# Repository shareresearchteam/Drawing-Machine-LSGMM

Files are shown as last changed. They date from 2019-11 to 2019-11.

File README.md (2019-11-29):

# LSGMM (Large-Scale Generative Mark Maker) Project Open-Source Repository

This machine provides the foundation for a human-robot interaction study that examines viewer interest with respect to process-centric and audience-modifiable abstract drawings.  A minimalistic design approach was used to highlight the aesthetic effect of the drawing and the machine’s motion as opposed to its visual presence.  Viewer interaction will manifest in slight, yet immediate and identifiable marks that stitch together a piece over the course of days or even weeks.  Witnessing the arc of a macroscopic structure appear, and the microscopic contributions from past viewers, is fundamental to the research, and the installation as a whole.

Drawing machines, and hanging pen plotters in particular, have been widely implemented by both the art and maker communities.  Harvey Moon’s work integrated satellite images to stitch together map-based abstractions in a similar exhibit.  Mechanically, we look to expand on existing designs by detailing a more scalable infrastructure.  In terms of interaction, we aim to hone the balance between viewer agency and structure.  Inspiration has been taken both from founders of the generative art movement (Manfred Mohr, Frieder Nake) and traditional contemporary abstractionist (Agnes Martin, Ellsworth Kelly, Eva Hesse, Sol Lewitt).  Subsequent works will examine both the mechanical and algorithmic sources of randomness and imperfection to repeated marks.

The current design serves as a baseline for the project goals described above.  It is our hope that others with overlapping goals can utilize or build on the open source software and hardware.

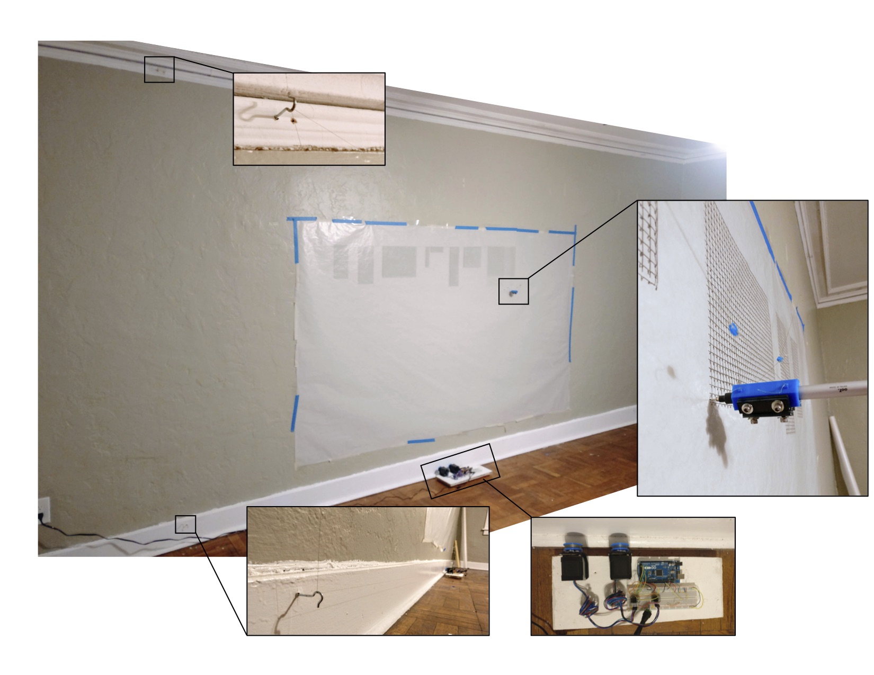
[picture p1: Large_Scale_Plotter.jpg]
Title


## File Guide

**Code Base**:
- Code base used to program Teensy 3.5 micro-controller via the Arduino IDE.  The setup and loop functions are located within the main file LSGMM_code.ino.  The code for the 'Bezier Node' drawing can be found in the node_bezier_alg.ino file.  The code for the 'Worn Structure' drawing can be found in the worn_structue.ino file.
- Libraries used within the LSGMM code base.  Add these to the Library Arduino folder before compilation.

**Hardware Assembly**:
- 3D print models used in LSGMM hardware.  Fusion 360 and .stl files available for all parts.
- Basic assembly instructions
- Bill of Materials 

**Media**:
- Exhibition drawing images of the two designs ('Bezier Node' and 'Worn Structure') from the study exhibitions.
- Introductory project video 

## Reference

A. Phillips, N. Fitter, and A Vinoo, "May I Draw Your Attention?  Initial Lessons from the Large-Scale Generative Mark Maker", Under review for publication in Robotics and Automation Letters (RA-L) and presentation at the 2019 IEEE International Conference on Robotics and Automation (ICRA).

* **Aidan Phillips** - aidan.instance@gmail.com []()
* **Naomi T. Fitter** - naomi.fitter@oregonstate.edu[]()
* **Ashwin Vinoo** - vinooa@oregonstate.edu[]()

## License

This project is licensed under the MIT License - see the [LICENSE.md](LICENSE.md) file for details

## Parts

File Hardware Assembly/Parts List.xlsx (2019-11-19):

Part Description | Purchase Site | QNT | Supplier
NEMA 17 Motors | link (https://www.amazon.com/Stepper-Bipolar-Connector-compatible-Printer/dp/B00PNEQKC0) | 2 | Amazon
ustepper driver | link (https://www.amazon.com/gp/product/B07JPJK8BZ/ref=ppx_yo_dt_b_asin_title_o00__o00_s00?ie=UTF8&psc=1) | 1 | Amazon
Motor dampeners | link (https://www.amazon.com/Rubber-Stepper-Vibration-Damper-Screws/dp/B07415B39B) | 1 | Amazon
Teensy 3.5 uC | link (https://www.digikey.com/product-detail/en/sparkfun-electronics/DEV-14056/1568-1464-ND/6569368) | 1 | Digikey
Shaft Mounting Hub | link (https://www.amazon.com/gp/product/B00KRJAPP4/ref=ox_sc_act_title_1?smid=A333XEUDSX4WY3&psc=1) | 2 | Amazon
Motor right angle brackets | link (https://www.amazon.com/gp/product/B071NWWB7Z/ref=ppx_yo_dt_b_asin_title_o02__o00_s02?ie=UTF8&psc=1) | 1 | Amazon
String | link (https://www.cabelas.com/product/WESTERN-FILAMENT-TUFF-LINE-XP/2972406.uts?productVariantId=6126147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) | 1 | Cabela's
12 V 5A DC PSU | link (https://www.ebay.com/itm/Quality-12V-5A-5-amp-60W-DC-POWER-Supply-ADAPTER-Transformer-LED-Strip-CCTV-PC/123067454133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) | 1 | Amazon

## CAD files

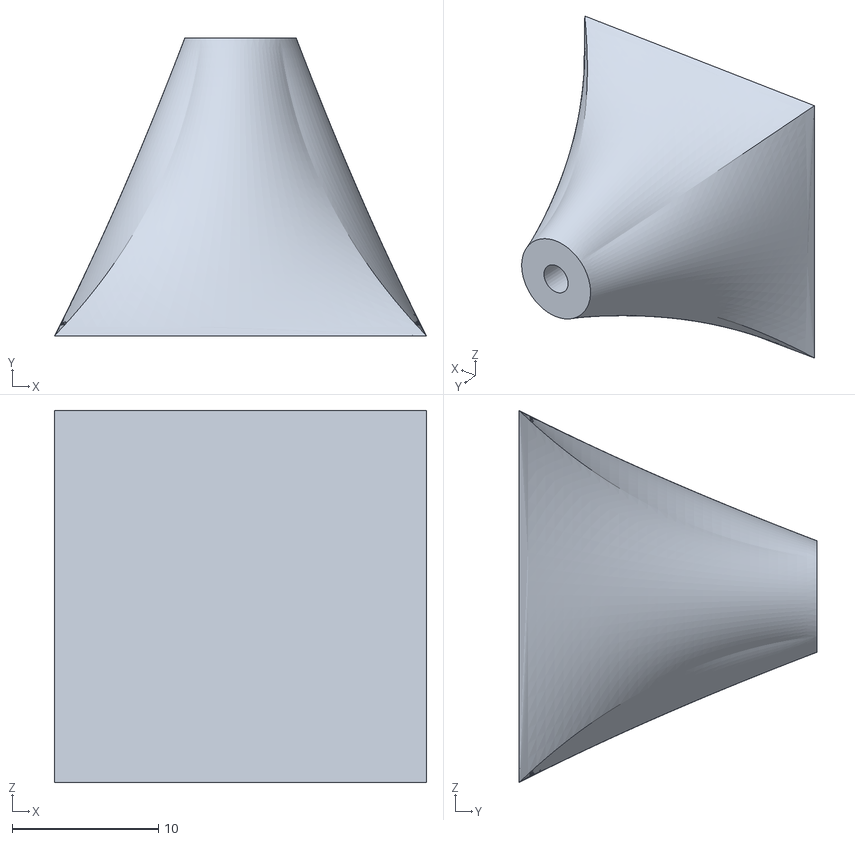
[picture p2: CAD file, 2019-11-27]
Hardware Assembly/3D Print Models/EyeHook Holders.stl
25.4 x 20.3 x 25.4

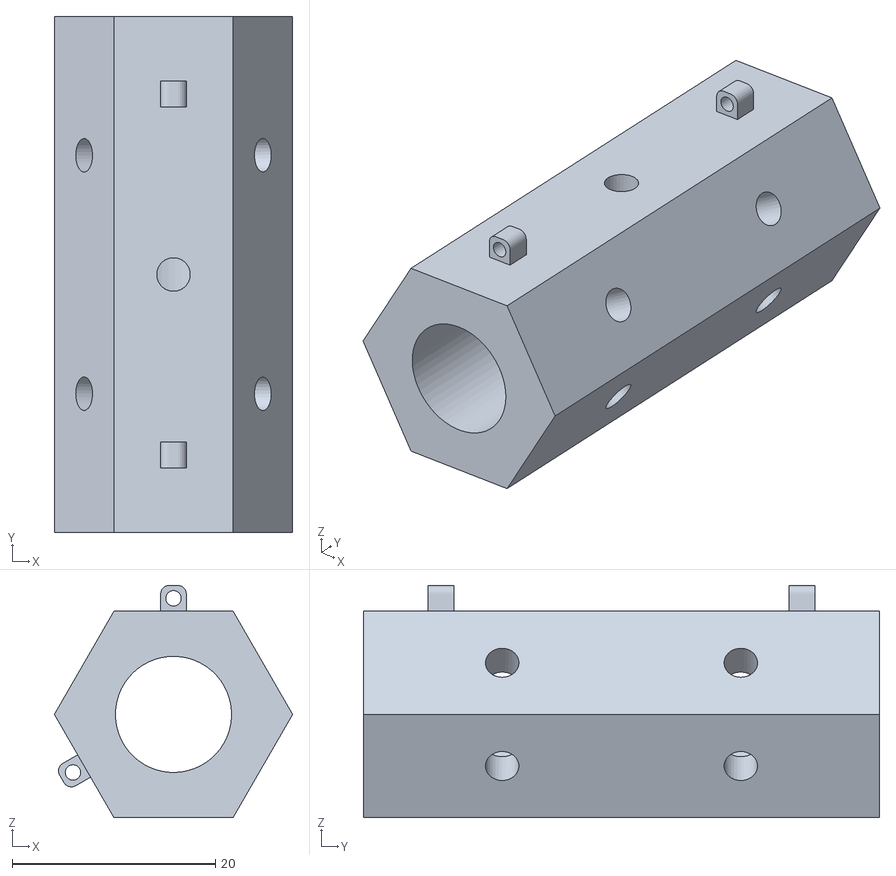
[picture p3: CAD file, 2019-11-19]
Hardware Assembly/3D Print Models/Pen_Holder.stl
23.5 x 50.8 x 22.9

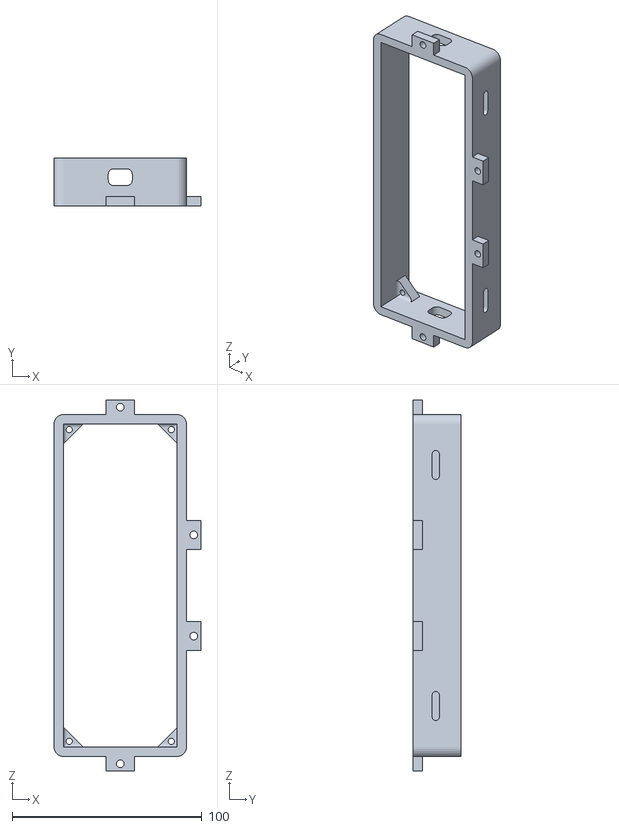
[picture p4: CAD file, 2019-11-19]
Hardware Assembly/3D Print Models/Electronics_Enclosure.stl
77.5 x 25.4 x 195.6

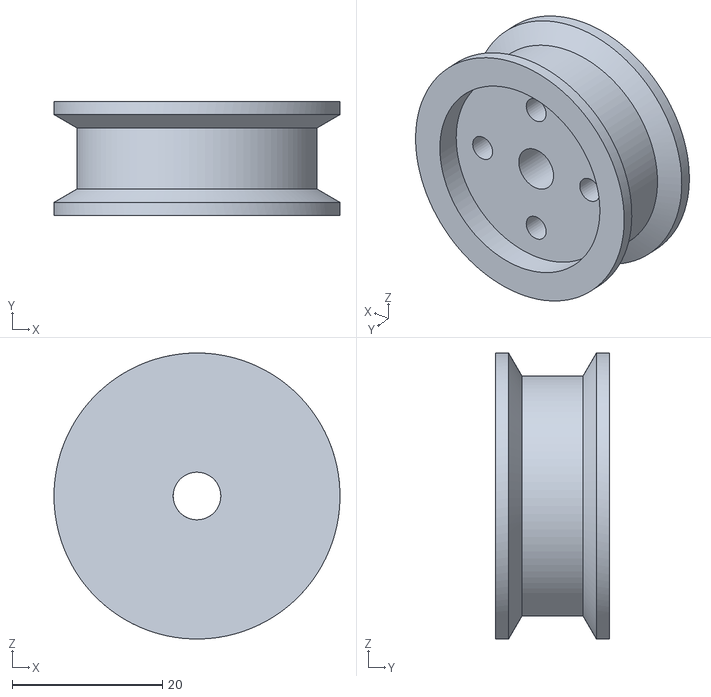
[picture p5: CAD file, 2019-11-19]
Hardware Assembly/3D Print Models/Spool.stl
38.1 x 15.2 x 38.1

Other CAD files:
Hardware Assembly/3D Print Models/Electronics_Enclosure.f3d
Hardware Assembly/3D Print Models/EyeHook Holders.f3d
Hardware Assembly/3D Print Models/Pen_Holder.f3d
Hardware Assembly/3D Print Models/Spool.f3d

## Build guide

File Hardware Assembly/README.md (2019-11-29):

## Hardware Assembly Basics

1. Aquire parts similar or equal to that on the 'Parts List' spread sheet

2. From the '3D Print Models' Folder print out:
	a) 2 Spools
        b) 1 Pen holder
	c) 4 Eyehook mounts
        c) 1 Electronics enclosure (optional)

3. Fix the stepper motor brackets and electronics enclosure onto a piece of wood or any other suitable base plate.

4. Fix the stepper dampers (with two screws only per motor) to the motor brackets.

5. Fix the stepper motors to the stepper dampers (with two screws only per motor).

6. Connect the stepper motor driver to the micro-controller by referencing the pin definitions in the LSGMM.ino file.

7. Complete other electrical connections by referencing the motor driver and micro-controller datasheets.

8. Mount the 4 eyehook mounts to a wall surface with a double sided adhesive and screw in eyehooks.

9. Fix hubs to spools and mount onto motor shaft with hub set screw.

10. Route two lengths of fishing line, one per spool, on left and right side eye hooks.  

11. Tie string on each spool, and dab with super glue.

12. Thread string through pen holder holes and re-tie on each side.  Rubber washers can fix this string length such that the pen is balanced and perpendicular to the wall surface.

13. Center the pen to a desired location and measure the string lengths.  Input these initial conditions into the LSGMM.ino file and run the cal_menu() function in the void setup().

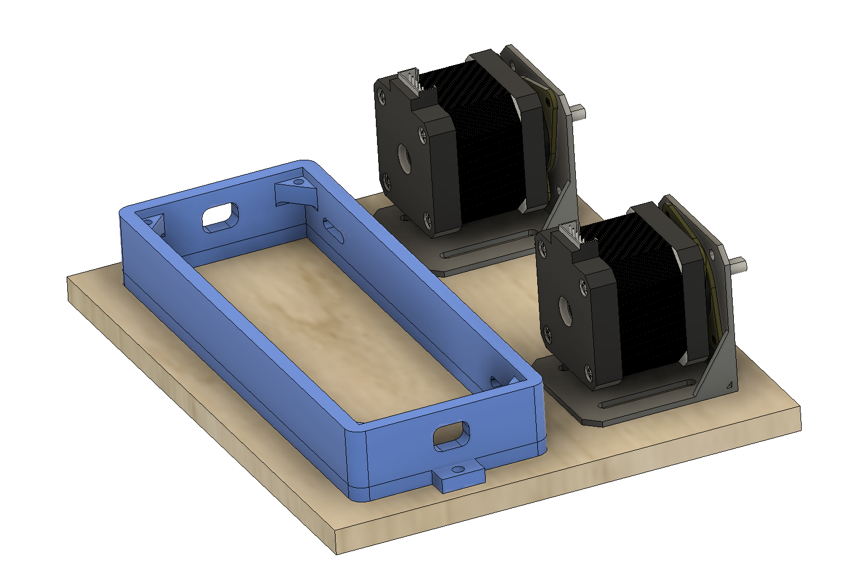
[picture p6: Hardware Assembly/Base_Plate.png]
Title


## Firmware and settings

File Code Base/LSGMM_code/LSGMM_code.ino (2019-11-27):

#include <TMC2130Stepper.h>
#include <Gaussian.h>
#include <HX711.h>
#include <SD.h>
#include <SPI.h>
#include <Servo.h>

//#include <Encoder.h>

#define unit_num_1 1
#define unit_num_2 0
#define unit_num_3 0

// Motor Driver SPI Pins
// RM = Right Motor, LM = Left Motor
#if unit_num_1
#define DIR_PIN_RM     6
#define STEP_PIN_RM    5
#define CS_PIN_RM      4
#define DIR_PIN_LM     25
#define STEP_PIN_LM    24
#define CS_PIN_LM      2
#elif unit_num_2
#define DIR_PIN_RM     2
#define STEP_PIN_RM    1
#define CS_PIN_RM      8
#define DIR_PIN_LM     19
#define STEP_PIN_LM    20
#define CS_PIN_LM      7
#elif unit_num_3
#define DIR_PIN_RM     9
#define STEP_PIN_RM    8
#define CS_PIN_RM      7
#define DIR_PIN_LM     6
#define STEP_PIN_LM    5
#define CS_PIN_LM      4
#endif

// Enable pins grounded on both drivers, 19 is arbitrary
#define EN_PIN        17

#define DOUT1  33
#define CLK1  34
#define DOUT2  51
#define CLK2  52
const long LOADCELL_OFFSET  =  10682624;
const long LOADCELL_DIVIDER =  5895655;
HX711 loadCell_1;
HX711 loadCell_2;
Servo servo1;

//Encoder enc_left(19, 18);
//Encoder enc_right(20, 21);

#define usteps        256

// Initial Conditions (inches):
//************************************************
#define LM_initial_length     50//86//95
#define RM_initial_length     50//86//95
#define seperation_distance   60//162//186
#define step_rate_lm          (.0314159 * 0.75) // (radians/fullstep) * radius = arclength/fullstep
#define step_rate_rm          (.0314159 * 0.75) // corresponds to amount of string released per full step
// ***********************************************

#define spd  500  // Minimum microsecond delay between usteps, should be changed when usteps is changed

TMC2130Stepper driver1 = TMC2130Stepper(EN_PIN, DIR_PIN_LM, STEP_PIN_LM, CS_PIN_LM);
TMC2130Stepper driver2 = TMC2130Stepper(EN_PIN, DIR_PIN_RM, STEP_PIN_RM, CS_PIN_RM);

long lms = 0;  // Global variable that stores left motor string length in usteps
long lmss = 0;
long lmf = 0;  // Global variable that stores left motor encoder pulses converted to usteps
long rms = 0;  // Global variable that stores right motor string length in usteps
long ll_init;  // Global variable that stores initial left motor string length in usteps
long lr_init;  // Global variable that stores initial right motor string length in usteps

double x_init; // Global variable that stores initial cartesian x-coordinate in inches
double y_init; // Global variable that stores initial cartesian y-coordinate in inches

int ang_max = 160;
int ang_min = 150;

double SD_x = 0;
double SD_y = 0;

double sdx_prev = 0;
double sdy_prev = 0;

// Number of nodes in node bezier algorithm
#define n_nodes   2300
#define max_n  200
Gaussian myGaussian(85, 27);  // Initialize Gaussian RV -> (mean, variance)

File myFile;

void setup() {

  Serial.begin(19200);

  SPI.begin();
  pinMode(MISO, INPUT_PULLUP);

  driver1.begin();            // Initiate pins and registeries
  driver1.rms_current(450);   // Set stepper current
  driver1.stealthChop(1);     // Enable extremely quiet stepping
  driver2.begin();            // Initiate pins and registeries
  driver2.rms_current(450);   // Set stepper current to
  driver2.stealthChop(1);     // Enable extremely quiet stepping

  driver1.microsteps(usteps);
  driver1.interpolate(0);
  driver2.microsteps(usteps);
  driver2.interpolate(0);

  loadCell_1.begin(DOUT1, CLK1);
  loadCell_1.set_scale(LOADCELL_DIVIDER);
  loadCell_1.set_offset(LOADCELL_OFFSET);
  loadCell_1.tare();

  loadCell_2.begin(DOUT2, CLK2);
  loadCell_2.set_scale(LOADCELL_DIVIDER);
  loadCell_2.set_offset(LOADCELL_OFFSET);
  loadCell_2.tare();
  servo1.attach(23);
  lift(1);

  x_init = return_X_pos();
  y_init = return_Y_pos();
  ll_init = round(LM_initial_length / (step_rate_lm / usteps));
  lr_init = round(RM_initial_length / (step_rate_rm / usteps));


  /*Serial.print("Initializing SD card...");
    if (!SD.begin(BUILTIN_SDCARD)) {
    Serial.println("initialization failed!");
    //while(1){} // prevent from progressing if no SD card
    }
    Serial.println("initialization done.");*/

  //***********************************************


  cal_menu();   // Calibration Routine, Guided by serial commands
  //bez_node(); // ----------------------> Bezier DRAWING
  //ws();       // ----------------------->  Worn Structure DRAWING
}

void loop() {

}

// Function that returns the number of steps needed for the left motor to reach
// the input coordinates (x,y) from current pen positions.  A negative step number
// corresponds to string retraction, while positive is extension.
long position_Request_LM(double x, double y) {
  long stepNum_LM;        // Relative length in steps
  double desiredLength;   // Absolute length in inches
  long desiredSteps;      // Absolute length in usteps
  desiredLength = x / (cos(atan(y / x)));  // Coordinate Transform from cartesian to left length
  desiredSteps = round(desiredLength / (step_rate_lm / usteps));
  stepNum_LM = desiredSteps - (lms + ll_init);
  return stepNum_LM;
}

// Function that returns the number of steps needed for the right motor to reach
// the input coordinates (x,y) from current pen positions.  A negative step number
// corresponds to string retraction, while positive is extension.
long position_Request_RM(double x, double y) {
  long stepNum_RM;        // Relative length in steps
  double desiredLength;   // Absolute length in inches
  long desiredSteps;      // Absolute length in usteps
  desiredLength = y / (sin(atan(-y / (x - seperation_distance))));  // Coordinate Transform from cartesian to right length
  desiredSteps = round(desiredLength / (step_rate_rm / usteps));
  stepNum_RM = desiredSteps - (rms + lr_init);
  return stepNum_RM;
}

// Function that adjusts timing such that both motors stop moving at the same time.
// Direction and step instructions are then sent to the motor drivers.  Due to the
// coordinate system, linear motion does not occur by calling this function.
void motorStep(double x, double y, double stepSpeed) {

  //lmf = round((double)enc_left.read()*2.0*3.14159265*.51/2400.0 / (step_rate_lm / usteps));  // convert enoder pulses to drive spool micro steps
  //long lme = lms - lmf; // error signal

  /*Serial.println(lms);
    Serial.println(lmf);
    Serial.println(lme);
    Serial.println();*/

  //lms = -round((double)enc_left.read()  * 19.5);
  //rms = -round((double)enc_right.read() * 19.5);

  long stepNum_RM = position_Request_RM(x, y); //refresh stepNum_RM
  long stepNum_LM = position_Request_LM(x, y); //refresh stepNum_LM

  rms += stepNum_RM;  // update global length variables
  //lmss += stepNum_LM;
  lms += stepNum_LM;


  //printDouble(return_X_pos(), 3);
  //printDouble(return_Y_pos(), 3);

  /*Serial.println(lms);
    Serial.println(stepNum_LM);
    Serial.println(return_X_pos());
    Serial.println(return_Y_pos());
    Serial.println("");/*


    Serial.println(lms);
    Serial.println(stepNum_LM);
    Serial.println(return_X_pos());
    Serial.println(return_Y_pos());
    Serial.println("");*/

  //Serial.println(enc_left.read());


  if (stepNum_LM < 0) {
    digitalWrite(DIR_PIN_LM, LOW);
    stepNum_LM = stepNum_LM * -1;
  }
  else
    digitalWrite(DIR_PIN_LM, HIGH);

  if (stepNum_RM < 0) {
    digitalWrite(DIR_PIN_RM, HIGH);
    stepNum_RM = stepNum_RM * -1;
  }
  else
    digitalWrite(DIR_PIN_RM, LOW);


  unsigned long previousMillis1 = 0;
  unsigned long previousMillis2 = 0;
  unsigned long currentMillis;

  double setSpeed_adjusted1 = stepSpeed;
  double setSpeed_adjusted2 = stepSpeed;

  long count_RM = 0;
  long count_LM = 0;

  // The motor that has a larger amount of steps gets a longer amount of time
  //    between steps.  The minimum speed always remains spd (define statement)
  if (stepNum_LM > stepNum_RM) {
    setSpeed_adjusted1 = ((double)stepNum_LM / (double)stepNum_RM) * stepSpeed;
    setSpeed_adjusted2 = stepSpeed;
  }
  else if (stepNum_LM < stepNum_RM) {
    setSpeed_adjusted1 = stepSpeed;
    setSpeed_adjusted2 = ((double)stepNum_RM / (double)stepNum_LM) * stepSpeed;
  }


  // send commands to driver modules in asychnrnous timing scheme
  while (count_RM < stepNum_RM || count_LM < stepNum_LM) {
    currentMillis = micros();

    if ((currentMillis - previousMillis1 >= setSpeed_adjusted1) && count_RM < stepNum_RM) {
      digitalWrite(STEP_PIN_RM, LOW);
      previousMillis1 = currentMillis;
      count_RM++;
    }
    digitalWrite(STEP_PIN_RM, HIGH);

    currentMillis = micros();

    if ((currentMillis - previousMillis2 >= setSpeed_adjusted2) && count_LM < stepNum_LM) {
      digitalWrite(STEP_PIN_LM, LOW);
      previousMillis2 = currentMillis;
      count_LM++;
    }
    digitalWrite(STEP_PIN_LM, HIGH);


  }

  //lms = -round((double)enc_left.read()  * 19.5);
  //rms = -round((double)enc_right.read() * 19.5);

  //Serial.println(lmss - lms);
  //rms = rms - (lmss-lms);
  //lmss=lms;
}

// This functions performs an inverse coordinate transform on the global
// length variables to extract cartesian X position
double return_X_pos() {
  double l1 = (double)lms * step_rate_lm / usteps + LM_initial_length;
  double l2 = (double)rms * step_rate_rm / usteps + RM_initial_length;
  double x = (l1 * l1 - l2 * l2 + pow(seperation_distance, 2)) / (2 * seperation_distance);
  return x;
}

// This functions performs an inverse coordinate transform on the global
// length variables to extract cartesian Y position
double return_Y_pos() {
  double l1 = (double)lms * step_rate_lm / usteps + LM_initial_length;
  double x = return_X_pos();
  double y = sqrt(l1 * l1 - x * x);
  return y;
}

void sd_test() {

  //for (int k = 0; k < 10; k++) {
  myFile = SD.open("te.txt", FILE_WRITE);

  // if the file opened okay, write to it:
  if (myFile) {
    Serial.print("Writing to te.txt...");
    myFile.println("testing hi hi hi 1, 2, 3.");
    // close the file:
    myFile.close();
    Serial.println("done.");
  } else {
    // if the file didn't open, print an error:
    Serial.println("error opening test.txt");
  }

  // re-open the file for reading:
  myFile = SD.open("te.txt");
  if (myFile) {
    Serial.println("te.txt:");

    // read from the file until there's nothing else in it:
    while (myFile.available()) {
      Serial.write(myFile.read());
    }
    // close the file:
    myFile.close();
  } else {
    // if the file didn't open, print an error:
    Serial.println("error opening te.txt");
  }
  // }
}

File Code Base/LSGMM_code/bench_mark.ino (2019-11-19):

void print_menu() {

  Serial.println(       "t = Return Home"                 );
  Serial.println(       "y = star pattern for min step"   );
  Serial.println(       "u = Line at different speeds"    );
  Serial.println(       "i = filled rectangle"            );
  Serial.println(       "o = filled circle"               );
  Serial.println(       "b = lift compensation"           );
  Serial.println(       "a = move left"                   );
  Serial.println(       "s = move down"                   );
  Serial.println(       "w = move up"                     );
  Serial.println(       "d = move right"                  );
  Serial.println(       "= = increase aswd move dist"     );
  Serial.println(       "- = decrease aswd move dist"     );
  Serial.println(       "p = print current position"      );
  Serial.println(       "x = single step RM");
  Serial.println(       "z = single step LM dir 1"        );
  Serial.println(       "x = single step RM dir 1"        );
  Serial.println(       "c = single step LM dir 2"        );
  Serial.println(       "v = single step RM dir 2"        );
  Serial.println(       "m = print menu"                  );
  Serial.println(       "/ = deceleration test"           );
  Serial.println(       "[ = left motor signals"          );


}

void cal_menu() {
  char inChar = '`';
  double incr = .5;
  print_menu();

  while (1) {

    while (Serial.available() == 0)  {}
    inChar = (char)Serial.read();
    switch (inChar) {

      case 't':
        return_home();
        break;

      case 'y':
        Serial.println("Minimum Step, 'q' to quit");
        step_star();
        break;

      case 'u':
        Serial.println("Line at different speeds");
        line_speed();
        break;

      case 'i':
        Serial.println("Filled Rectangle");
        frect(return_X_pos(), return_Y_pos(), 1, 1); //randomDouble(1,3.5), randomDouble(1,3.5));
        break;

      case 'o':
        Serial.println("Filled Circle");
        circle_solid(return_X_pos(), return_Y_pos(), 1);
        break;

      case 'b':
        Serial.println("Lift Compensation");
        down();
        break;

      case 'a':
        motorStep(return_X_pos() - incr, return_Y_pos(), 300);
        break;

      case 's':
        motorStep(return_X_pos(), return_Y_pos() + incr, 300);
        break;

      case 'w':
        motorStep(return_X_pos(), return_Y_pos() - incr, 300);

        break;

      case 'd':
        motorStep(return_X_pos() + incr, return_Y_pos(), 300);
        break;

      case '=':
        incr += .05;
        Serial.println(incr);
        break;

      case '-':
        incr -= .05;
        Serial.println(incr);
        break;

      case 'p':
        Serial.println("-----------");
        printDouble(return_X_pos(), 5);
        printDouble(return_Y_pos(), 5);
        Serial.println("-----------");
        break;

      case 'x':
        //one_step_RM(1);
        motorStep(return_X_pos() + incr, return_Y_pos() + incr, spd);
        break;

      case 'z':
        //one_step_LM(1);
        motorStep(return_X_pos() - incr, return_Y_pos() - incr, spd);
        break;

      case 'v':
        one_step_RM(0);
        break;

      case 'c':
        one_step_LM(0);
        break;

      case 'm':
        print_menu();
        break;

      case '/':
        for (int i = 0; i < 10; i++) {
          motorStep(return_X_pos() + incr, return_Y_pos(), spd);
          motorStep(return_X_pos() - incr, return_Y_pos(), spd);
        }
        break;
      case '[':
        // Serial.println(Etest.read());
        Serial.println(lms);
        Serial.println();
        break;

      case '?':
        for(int i=0; i<5; i++){
          rr();
        }
        break;


        //break;
    }

  }
}


void step_star() {

  int full_steps = 1;
  int _spd = spd * 5;
  char inChar = '`';
  double incr = 15.0;

  while (inChar != 'q') {

    inChar = (char)Serial.read();

    if (inChar == '=') {
      full_steps++;
      Serial.println(full_steps);
    }
    else if (inChar == '-') {
      full_steps--;
      Serial.println(full_steps);
    }

    for (int i = 0; i < (usteps * full_steps); i++) {
      digitalWrite(STEP_PIN_RM, LOW);
      delayMicroseconds(_spd);
      digitalWrite(STEP_PIN_RM, HIGH);
    }
    delay(1000);

    for (int i = 0; i < (usteps * full_steps); i++) {
      digitalWrite(STEP_PIN_LM, LOW);
      delayMicroseconds(_spd);
      digitalWrite(STEP_PIN_LM, HIGH);
    }
    delay(1000);

    for (int i = 0; i < (usteps * full_steps); i++) {
      digitalWrite(STEP_PIN_RM, LOW);
      digitalWrite(STEP_PIN_LM, LOW);
      delayMicroseconds(_spd);
      digitalWrite(STEP_PIN_RM, HIGH);
      digitalWrite(STEP_PIN_LM, HIGH);
    }
    delay(1000);

    for (int i = 0; i < (usteps * full_steps); i++) {
      digitalWrite(STEP_PIN_RM, LOW);
      digitalWrite(STEP_PIN_LM, LOW);
      delayMicroseconds(_spd);
      digitalWrite(STEP_PIN_RM, HIGH);
      digitalWrite(STEP_PIN_LM, HIGH);
    }

    if (inChar == 't') {
      return_home();
      inChar = 'q';
    }

    delay(1000);
  }

}

void line_speed() {

  int _spd = spd;
  char inChar = '`';
  double yl = y_init;

  Serial.print("Current Speed = ");
  Serial.println(_spd);
  while (inChar != 'q') {


    _spd = lineSeg_ser_spd(x_init, yl, x_init + 5, yl, 0, _spd);
    yl += .2;
    _spd = lineSeg_ser_spd(x_init + 5, yl, x_init, yl, 0, _spd);
    yl += .2;

    Serial.println("Continue with another line?");
    while (Serial.available() == 0)  {}
    inChar = (char)Serial.read();

    if (inChar == 't') {
      return_home();
      inChar = 'q';
    }

    delay(1000);
  }

}

void return_home() {
  Serial.println("Returning Home");
  Serial.print(return_X_pos());
  Serial.print("  ");
  Serial.print(return_Y_pos());
  Serial.print("  -->  ");
  Serial.print(x_init);
  Serial.print("  ");
  Serial.println(y_init);
  motorStep(x_init, y_init, spd);
}

void one_step_LM(int dir) {
  if (dir == 0) {
    digitalWrite(DIR_PIN_LM, LOW);
    lms -= 1;
  }
  else if (dir == 1) {
    digitalWrite(DIR_PIN_LM, HIGH);
    lms += 1;
  }

  for (int i = 0; i < (usteps); i++) {
    digitalWrite(STEP_PIN_LM, LOW);
    delay(2);
    digitalWrite(STEP_PIN_LM, HIGH);
  }
}


void one_step_RM(int dir) {

  if (dir == 0) {
    digitalWrite(DIR_PIN_RM, HIGH);
    rms -= 1;
  }
  else if (dir == 1) {
    digitalWrite(DIR_PIN_RM, LOW);
    rms += 1;
  }
  for (int i = 0; i < (usteps); i++) {
    digitalWrite(STEP_PIN_RM, LOW);
    delay(2);
    digitalWrite(STEP_PIN_RM, HIGH);
  }

}

void down() {

  digitalWrite(DIR_PIN_RM, HIGH);
  digitalWrite(DIR_PIN_LM, HIGH);

  for (int i = 0; i < (usteps); i++) {
    digitalWrite(STEP_PIN_RM, LOW);
    digitalWrite(STEP_PIN_LM, LOW);
    delayMicroseconds(1300);
    digitalWrite(STEP_PIN_RM, HIGH);
    digitalWrite(STEP_PIN_LM, HIGH);
  }

}
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

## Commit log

2019-11-19 3D print files and parts list
    [Electronics_Enclosure.f3d, Electronics_Enclosure.stl, Parts List.xlsx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]
2019-11-25 Assembly Images
2019-11-27 assembly photo
2019-11-27 eyehook holder cad files
    [Eye-Hook Holders.stl, EyeHook Holders.f3d]
2019-11-29 file restructure
    [Parts List.xlsx]
2019-11-29 toc edits
    [Electronics_Enclosure.f3d, Electronics_Enclosure.stl, EyeHook Holders.f3d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]
